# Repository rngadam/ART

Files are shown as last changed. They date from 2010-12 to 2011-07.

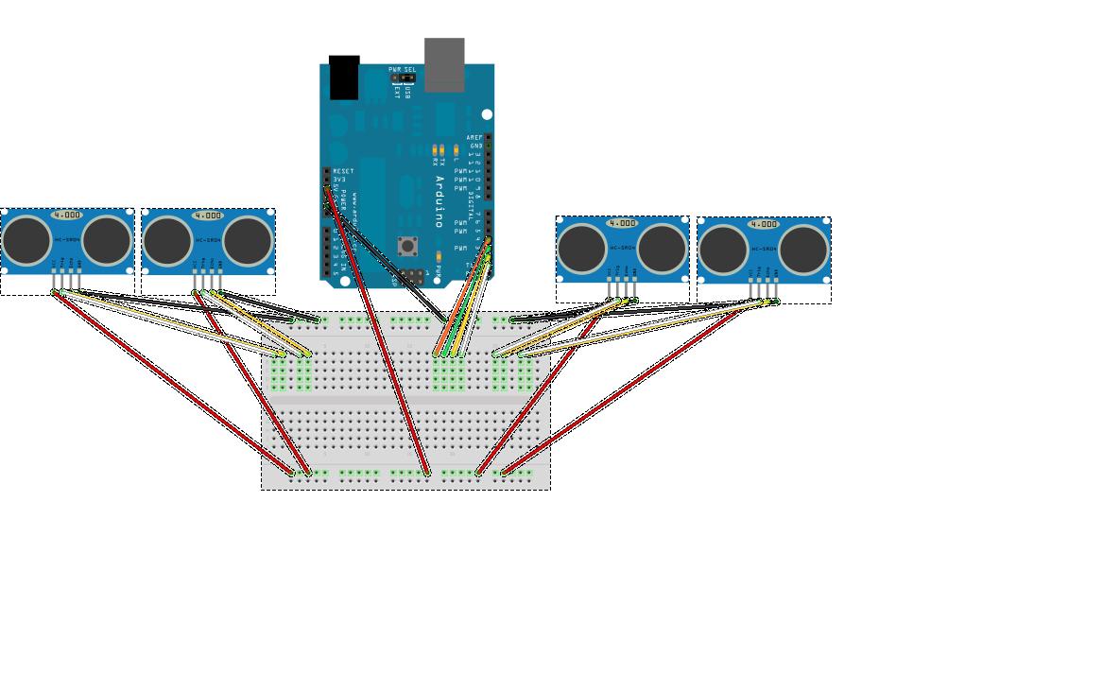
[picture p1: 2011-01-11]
ele/fritzing/ART-platform4_bb_20110103.jpg

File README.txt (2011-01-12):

Autonomous Robot Toy
http://www.xinchejian.com

Copyright 2011 Ricky Ng-Adam

   Licensed under the Apache License, Version 2.0 (the "License");
   you may not use this file except in compliance with the License.
   You may obtain a copy of the License at

       http://www.apache.org/licenses/LICENSE-2.0

   Unless required by applicable law or agreed to in writing, software
   distributed under the License is distributed on an "AS IS" BASIS,
   WITHOUT WARRANTIES OR CONDITIONS OF ANY KIND, either express or implied.
   See the License for the specific language governing permissions and
   limitations under the License.

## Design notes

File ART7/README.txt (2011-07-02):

Dependencies:

firmware:
	Arduino 22
	Android ADK release 0512

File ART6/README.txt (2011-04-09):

http://xinchejian.com

ART v6 (Autonomous Robot Toy)
Mechanical base: Remote control toy car
Motor control: microcontroller manipulation of the RC control
Sensors: five E18-D80NK infrared (obstacle detection, no distance ranging)
Computer: Arduino Uno
Characteristics: hacked inexpensive RC car, self-driving, forward and reverse fast interrupt-driven collision detection
Cost to build: ~425 RMB (~USD$65)
Code: https://github.com/rngadam/ART/tree/master/ART6
Video: http://v.youku.com/v_show/id_XMjU2NTQwMDky.html

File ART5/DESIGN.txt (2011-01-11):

ART5 (Autonomous Robot Toy version 5) combines the following:

- Mechanical four wheel vehicule based on a toy RC for propulsion and chassis
- Arduino Microcontroller  platform for communication and decisions
- CPLD for low-level sensor data acquisition and motor control
- RF communication to/from PC for debugging and visualization
- Processing-based dashboard on the PC.

RF communication solution is for telemetry and has been selected to be low-bandwidth, medium-range, low-power and inexpensive.

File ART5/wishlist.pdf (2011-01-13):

Receptacles

Type | Description | Details
Receptable Female Header 2.54mm DIP connector dual row | 9x2
Receptable Stackable Female Header 2.54mm DIP connector single row 8x1 Receptable Stackable Female Header 2.54mm DIP connector single row 6x1
Receptable DIP Socket Solder Tail | 18 pins
Receptable DIP Socket Solder Tail | 40 pins
Wires | Mini-JST Jumper cable (wires + male connector) | 2 wires
Wires | Mini-JST Jumper cable (wires + male connector) | 3 wires
Wires | Mini-JST Jumper cable (wires + male connector) | 4 wires
Wires | Mini-JST Jumper connector (female connector) | 2 wires
Wires | Mini-JST Jumper connector (female connector) | 3 wires
Wires | Mini-JST Jumper connector (female connector) | 4 wires
Connector
Wires | Heat-Shrink Tubing
Switch | Omron Snap Action Switch
Fastener | M3 nylon spacer
Fastener | M3 nylon screws
Fastener | M3 nylon washer
Fastener | M3 nylon nut
Fastener | M3 nylon standoff

Usage | Quantity | Example
RF transceiver RFC-1100A receptable | | http://www.alibaba.com/product-gs/283914360/Female_Header_2_54mm_DIP_connector/showimage.html
For custom Arduino shield | | http://www.alibaba.com/product-gs/285352058/2_54_mm_Single_Row_Female.html
For custom Arduino shield | | http://www.alibaba.com/product-gs/285352058/2_54_mm_Single_Row_Female.html
Socket for ATMega 328p | | http://toysdownunder.com/arduino/components/socket-plugs/18-pin-dip-socket.html
Socket for XC9536-DIP | | http://parts.digikey.com/1/parts/297142-40-pin-solder-tail-dip-socket-40-6518-10.html
Connect ground/vcc OR trigger/echo for HC-SR04
Connect ground/vcc/signal for infrared
Connect ground/vcc/trigger/echo
Connect ground/vcc OR trigger/echo for HC-SR04 Connect ground/vcc/signal for infrared
Connect ground/vcc/trigger/echo
Whiskers (collision detection) | | http://toysdownunder.com/arduino/components/action-switch.html
The spacers allows a constant gap between 2 components. http://www.bulte.com/gb/produits_fiche.cfm?id=1414&famille=entretoises

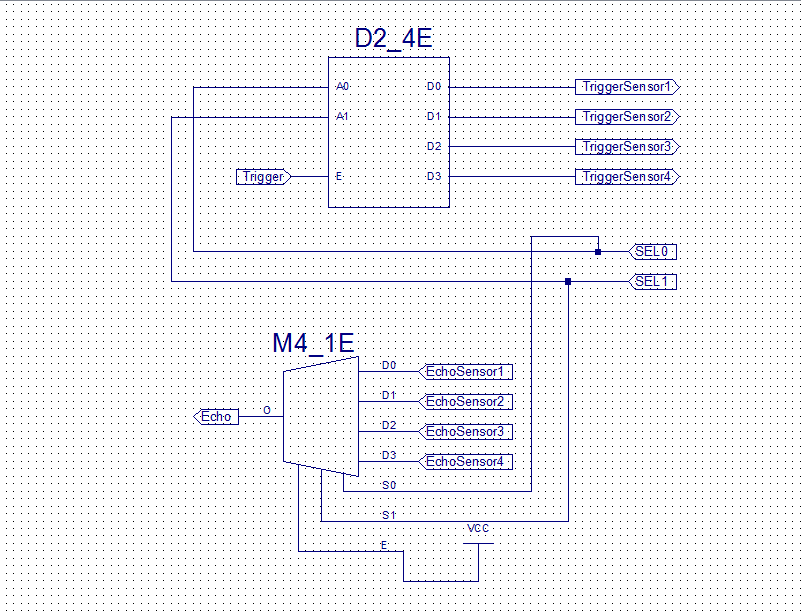
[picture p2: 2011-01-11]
ele/fritzing/UltrasonicDetector/schematic-sensor-selector.png

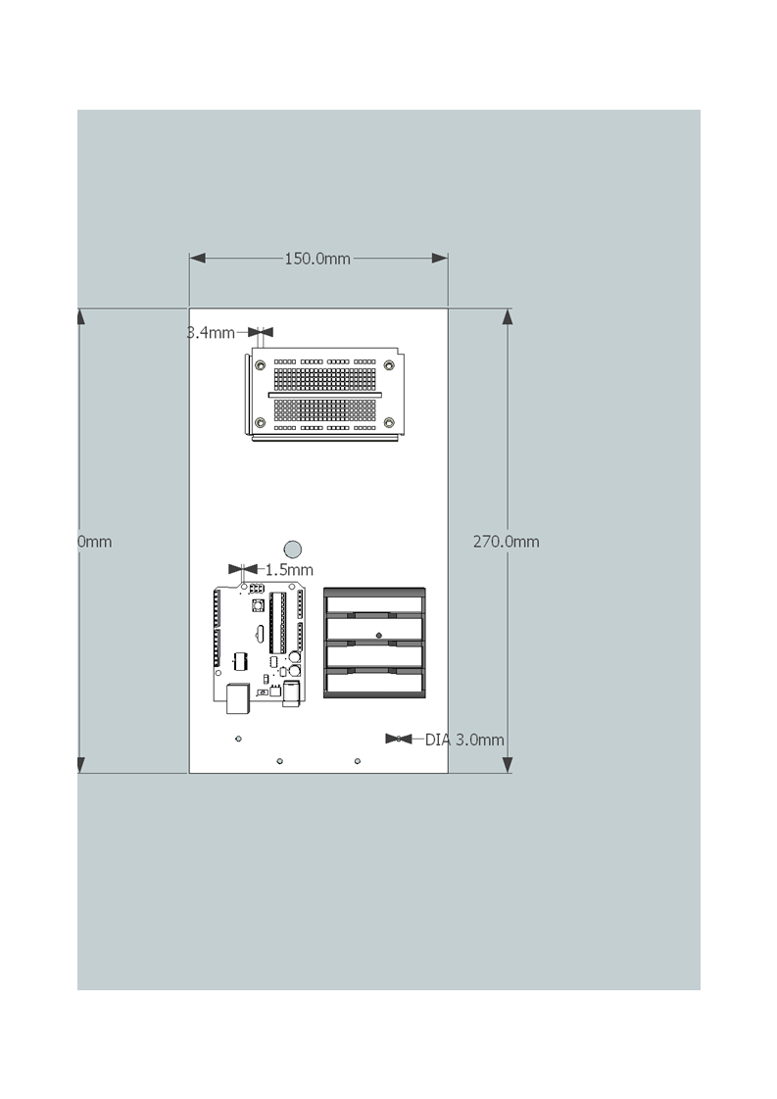
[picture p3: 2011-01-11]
mec/plate-v3_1.png

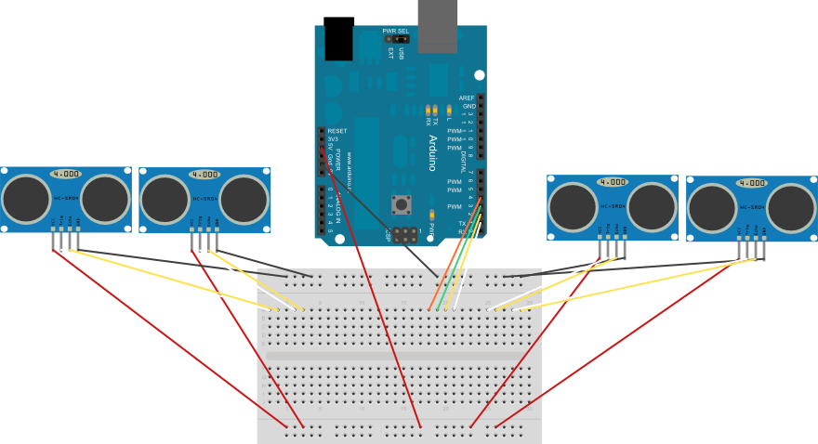
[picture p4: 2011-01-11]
ele/fritzing/ART-platform4_bb.png

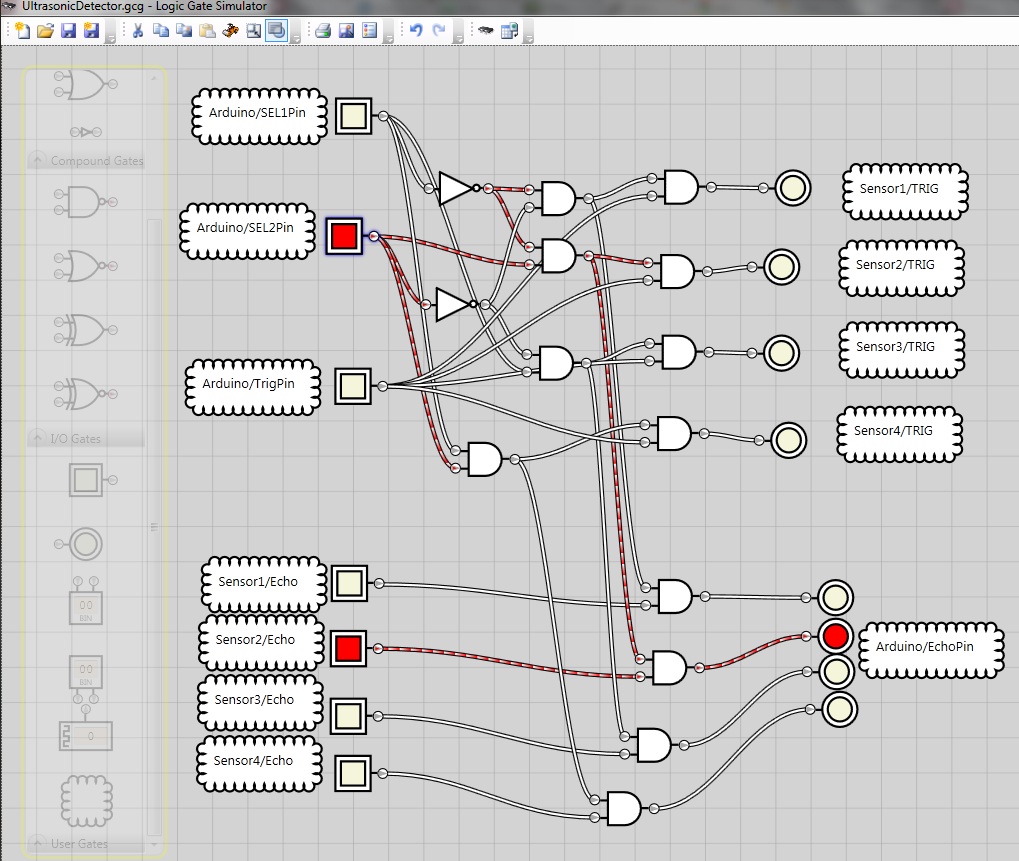
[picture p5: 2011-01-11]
ele/fritzing/UltrasonicDetector/UltrasonicDetectorLogic-LogicGateSimulator.jpg

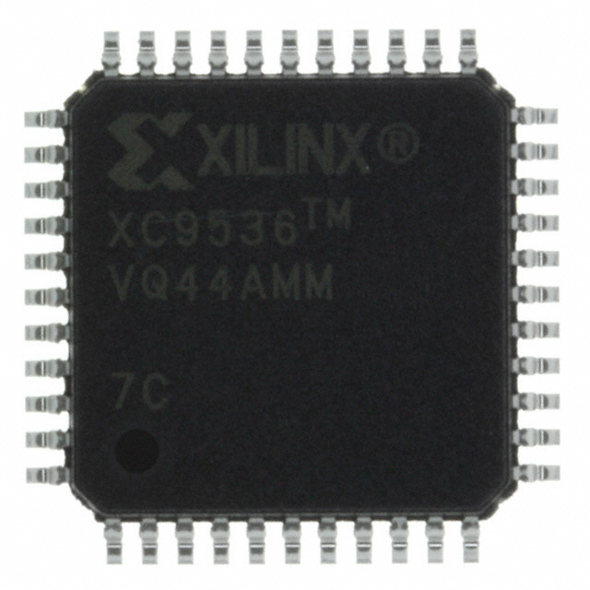
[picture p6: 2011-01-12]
ele/fritzing/XC9536-DIP/XC9536-7VQ44C.JPG

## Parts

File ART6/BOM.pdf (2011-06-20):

CAR

Description | Price/Unit | Quantity | Total
RC Toy Car (with 400mAh battery) | 67.00 | 1 | 67.00
Arduino Uno (with Atmega 328p) | 178.00 | 1 | 178.00
5 * Infrared sensors (E18-D80NK) | 30.00 | 5 | 150.00
Breadboard | 3.00 | 1 | 3.00
700mAh, 6V, Rechargeable NiCad | 15.00 | 1 | 15.00
Cabling and miscellaneous parts | 12.00 | 1 | 12.00
Total | | 64.3 | 425.00
| | USD | RMB

Source
http://item.taobao.com/item.htm?id=8549969961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

Datasheet

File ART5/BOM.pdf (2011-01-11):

CAR

Description | Price/Unit | Quantity | Total
RC Toy Car (with 400mAh battery) | 67.00 | 1 | 67.00
Arduino Uno (with Atmega 328p) | 178.00 | 1 | 178.00
CC1101 RF Transceiver with Power Amplifier | 70.00 | 1 | 70.00
4 * Ultrasonic sensors HC-SR04 | 37.00 | 4 | 148.00
4 * Infrared sensors E18-D80NK | 30.00 | 4 | 120.00
Xilinx XC9536 CPLD in a 40 DIP pin package | 42.00 | 1 | 42.00
Mini-breadboard | 3.00 | 1 | 3.00
700mAh, 6V, Rechargeable NiCad | 15.00 | 1 | 15.00
Cabling | 12.00 | 1 | 12.00
Motor shield (L298N) | 68.00 | 1 | 68.00
Arduino I/O expansion board | 48.00 | 1 | 48.00
Total | | 116.64 | 771.00
| | USD | RMB

Source
http://item.taobao.com/item.htm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

http://item.taobao.com/item.htm?id=8537476251http://item.taobao.com/item.htm?id=8537478635

Datasheet

http://iteadstudio.com/produce/cheap-cheap-ultrasonic-ranging-modulehc-sr04/

http://www.xilinx.com/support/documentation/xc9500.htm

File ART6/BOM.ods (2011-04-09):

Description | Price/Unit | Quantity | Total | Source | Datasheet
RC Toy Car (with 400mAh battery) | 67.00 | 1 | 67.00 | http://item.taobao.com/item.htm?id=7905841099
Arduino Uno (with Atmega 328p) | 178.00 | 1 | 178.00 | http://item.taobao.com/item.htm?id=8597883697
5 * Infrared sensors (E18-D80NK) | 30.00 | 5 | 150.00 | http://item.taobao.com/item.htm?id=8549969961
Breadboard | 3.00 | 1 | 3.00
700mAh, 6V, Rechargeable NiCad | 15.00 | 1 | 15.00
Cabling and miscellaneous parts | 12.00 | 1 | 12.00
Total |  | 64.3 | 425.00
 |  | USD | RMB

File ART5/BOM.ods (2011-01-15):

Description | Price/Unit | Quantity | Total | Source | Datasheet
RC Toy Car (with 400mAh battery) | 67.00 | 1 | 67.00 | http://item.taobao.com/item.htm?id=7905841099
Arduino Uno (with Atmega 328p) | 178.00 | 1 | 178.00 | http://item.taobao.com/item.htm?id=8597883697
RFC1100-A CC1101 RF Transceiver with Power Amplifier | 70.00 | 1 | 70.00 | http://item.taobao.com/item.htm?id=1914378907
4 * Ultrasonic sensors HC-SR04 | 37.00 | 4 | 148.00 | http://item.taobao.com/item.htm?id=3097091977 | http://iteadstudio.com/produce/cheap-cheap-ultrasonic-ranging-modulehc-sr04/
4 * Infrared sensors E18-D80NK | 30.00 | 4 | 120.00 | http://item.taobao.com/item.htm?id=8549969961
Xilinx XC9536 CPLD in a 40 DIP pin package | 42.00 | 1 | 42.00 | http://item.taobao.com/auction/item_detail.htm?item_num_id=5823204564 | http://www.xilinx.com/support/documentation/xc9500.htm
Mini-breadboard | 3.00 | 1 | 3.00
700mAh, 6V, Rechargeable NiCad | 15.00 | 1 | 15.00
Cabling | 12.00 | 1 | 12.00
Motor shield (L298N) | 68.00 | 1 | 68.00 | http://item.taobao.com/item.htm?id=8537476251
Arduino I/O expansion board | 48.00 | 1 | 48.00 | http://item.taobao.com/item.htm?id=8537478635
Total |  | 116.64 | 771.00
 |  | USD | RMB

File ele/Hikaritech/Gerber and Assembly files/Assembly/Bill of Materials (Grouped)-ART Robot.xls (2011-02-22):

Designator | Description | Comment | Footprint | Value | Quantity
C1 | Solid Aluminum Capacitor with Organic Semiconductor Electrolyte: 22uF, 25V, Bulk Pack | 25V | E | 22uF | 1
C2 | Solid Aluminum Capacitor with Organic Semiconductor Electrolyte: 100uF, 16V, Bulk Pack | 16V | E | 100uF | 1
C3, C4 | Dipped Radial Multilayer Ceramic Capacitor X7R: 100nF | VP41BY104 | VP41-2.5 | 100nF | 2
P1 | CONN 2 PINS 2.54mm Wire to Board Latch RA Tin | Battery Input | HDR1X2H |  | 1
P2, P3 | Header, 6-Pin | Arduino Header, Arduino Header Analog | HDR1X6 |  | 2
P4, P15 | Header, 8-Pin | Arduino Header Digital | HDR1X8 |  | 2
P5 | Header, 20-Pin, Dual row | CPLD Header DIP 40 | DIP-40 |  | 1
P6, P8, P10, P13 | CONN 3 PINS 2.54mm Wire to Board Latch RA Tin | IBH, IFH, ILH, IRH | HDR1X3H |  | 4
P7, P9, P11, P14 | CONN 4 PINS 2.54mm Wire to Board Latch RA Tin | UBH, UFH, ULH, URH | HDR1X4H |  | 4
P12, P17, P18, P19 | Header, 3-Pin | SBH, SFH, SLH, SRH | HDR1X3H |  | 4
P16 | Header, 9-Pin, Dual row | RFC-1100A | Module RF |  | 1
P20 | Header, 3-Pin, Dual row | Select | HDR2X3 |  | 1
R1, R2, R3, R4, R5, R6, R7 | Resistor | Res1 | AXIAL-0.3 | 1K | 7
U1 | Positive-Voltage Regulator | µA7805CKC | KC03 |  | 1

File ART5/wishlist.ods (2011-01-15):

Type | Description | Details | Usage | Quantity | Example
Receptable | Female Header 2.54mm DIP connector dual row | 9x2 | RF transceiver RFC-1100A receptable |  | http://www.alibaba.com/product-gs/283914360/Female_Header_2_54mm_DIP_connector/showimage.html
Receptable | Stackable Female Header 2.54mm DIP connector single row | 8x1 | For custom Arduino shield |  | http://www.alibaba.com/product-gs/285352058/2_54_mm_Single_Row_Female.html
Receptable | Stackable Female Header 2.54mm DIP connector single row | 6x1 | For custom Arduino shield |  | http://www.alibaba.com/product-gs/285352058/2_54_mm_Single_Row_Female.html
Receptable | DIP Socket Solder Tail | 18 pins | Socket for ATMega 328p |  | http://toysdownunder.com/arduino/components/socket-plugs/18-pin-dip-socket.html
Receptable | DIP Socket Solder Tail | 40 pins | Socket for XC9536-DIP |  | http://parts.digikey.com/1/parts/297142-40-pin-solder-tail-dip-socket-40-6518-10.html
Wires | Mini-JST Jumper cable (wires + male connector) | 2 wires | Connect ground/vcc OR trigger/echo for HC-SR04
Wires | Mini-JST Jumper cable (wires + male connector) | 3 wires | Connect ground/vcc/signal for infrared
Wires | Mini-JST Jumper cable (wires + male connector) | 4 wires | Connect ground/vcc/trigger/echo
Wires | Mini-JST Jumper connector (female connector) | 2 wires | Connect ground/vcc OR trigger/echo for HC-SR04
Wires | Mini-JST Jumper connector (female connector) | 3 wires | Connect ground/vcc/signal for infrared
Wires | Mini-JST Jumper connector (female connector) | 4 wires | Connect ground/vcc/trigger/echo
Connector
Wires | Heat-Shrink Tubing
Switch | Omron Snap Action Switch |  | Whiskers (collision detection) |  | http://toysdownunder.com/arduino/components/action-switch.html
Fastener | M3 nylon spacer |  | The spacers allows a constant gap between 2 components. |  | http://www.bulte.com/gb/produits_fiche.cfm?id=1414&famille=entretoises
Fastener | M3 nylon screws
Fastener | M3 nylon washer
Fastener | M3 nylon nut
Fastener | M3 nylon standoff

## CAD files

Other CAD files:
mec/robot-car-base-plate-with-arduino-v2.skp
mec/robot-car-base-plate-with-arduino-v3.skp
mec/robot-car-base-plate-with-arduino.skp
mec/robot-car-base-plate.skp

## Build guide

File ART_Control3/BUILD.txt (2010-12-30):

To build this robot toy car, you will need:

Components:

* an RC car (67RMB, http://item.taobao.com/item.htm?id=7905841099)
* an additional battery (to the one that comes with the RC car) rechargeable Ni-Cd 400mAh/6V battery pack 
* an Arduino (any should do, we use the Dueminalove)
* a pile of cables with pins
* one or more ranging sensor of some kind (infrared such as Sharp IR or Ultrasonic such as the Parallax Ping or both)
* a small breadboard
* an IC with at least 4 transistors (such as the ULN2803APG) or 4 separate NPN transistors 
* two AA battery (to test the RF transmitter)

Tools:
* a USB cable (standard USB transfer cable)
* a PC (Mac, Linux or Windows)
* Arduino software
* a Dremel (or its Chinese copy equivalent...)
* a wire stripper
* a marker (Sharpie fine point permanent marker)
* a right angle ruler
* a set of precision screwdrivers
* some electric tape (or alternatively, little name stickers...)
* four plastic bags for the screws you'll remove
* a soldering iron 
* a ballpen
* cardboard box at least 15cm X 25cm (surface to put the woodboard on top to drill holes)
* a camera for posterity!

Optional
* possibly a small servo-motor to rotate ranging sensor

Steps:

Charge your batteries 
* move to the next few steps that don't require battery while you wait (4 hours charge time)

Remove the plastic shell from the top of the car
* Turn over and start unscrewing starting with the back of the car
* Note that you may have to unscrew at an angle to get the screws furthest back out
* Keep the screws securely in a bag, organized by step (write down where they came from with the marker)
* You will find 4 screws on the main plate, 2 in front, 2 for the lights
* Get the antenna out of the shell (don't pull out too quickly - watch out for those thin wires connecting to the light)
* Put the shell on the side
* Remove the hot glue by melting it with soldering iron and a pair of tweezers 
* Remove the useless soundbox plastic cover box on top of the servo (3 screws)
* Screw the lights upside-down on the servo plastic box now available holes
* Tape the electric wires from the light to the plastic chassis

Test your car with the provided RF remote to verify that it does indeed still work

Take apart the remote
* twist the round plastic piece securing the antenna
* remove screws to open the case (6 screws)
* remove the screws holding down the board
* take care to mark which wire goes to source and ground (ex: the wire to positive marked the marker)
* unscrew the antenna

Create a new wood plate by tracing the various components and holes (don't forget the hole for the antenna)
* Dimension: 15cm wide by 25cm long (size of wood board is chosen to fit the board within the wheels)
* Use the right angle ruler: create an angle, measure desired width and height, trace box with marker

Remove the plastic plate on which the plastic shell was screwed
* Remove the four screws and then squeeze the hinges on the front of the plate to remove

Do the layout
* Figure out where to put the holes by overlaying the plastic plate on the board 
* To locate holes, remove the ballpoint from the pen body  
* Take all the electric components and place them on the new plate until satisfied with the layout
* Trace screwholes and the outline of parts for electronics
* Don't forget to leave a larger hole on the front of the plastic plate and to the left for the antenna to come out!
* Create a grid of holes in front and in the back of the board to give you flexibility in placing the sensors

Cut the wood plate with the dremel
* Cut rectangle with the Dremel and than break if off
* Sand edges of rectangle

Drill holes into the wood plate with the dremel 
* use a spare piece of wood or cardboard box upside-down
* put the wood board on the cardboard box
* drill holes!
* Verify alignment with plastic plate of chassis
* Test alignment with antenna

Assemble mechanical parts
* Put back the plastic plate on the car
* Tie-wrap the wood board to the plastic plate
* Tie-wrap the components to the wood board

Assemble electronics
* Connect wires to/from the various components (except the battery)
* Strip the wire from the transmitter and push the wire filaments in the breadboard using the wires with pin
* If possible, use consistent wires (white or yellow for signal, black or blue for ground, red or orange for power)

Place the sensor(s)
* Make sure the sensors are physically secure (they tend to move when the robot hit something...)

Write basic Arduino program
* Start Arduino IDE
* Write basic Arduino program
* Connect to USB
* Upload

Test your robot
* transmitter light comes on 
* sensor obstacle detection works
* Test that motor control works
* Turn on the car, manually trigger the sensor
* Put it on the ground and let it fly! (don't forget to get it on video!)

Next step
* Use version control (github.com or code.google.com) to keep source and documentation
* When a version (kinda) does something interesting, commit to source control and explain observed behavior
                
Future
* Mount electronic parts on motherboard stands (?)
* Create a working RF transmitter that can talk to the receiver
* Design and get PCB done (integrating power connection, switches, etc)
* Design and get aluminium plate done

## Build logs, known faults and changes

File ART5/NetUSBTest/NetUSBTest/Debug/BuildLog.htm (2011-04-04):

Build Log

| | Build started: Project: NetUSBTest, Configuration: Debug|Win32

Command Lines

Creating temporary file "c:\Users\rngadam\ART\ART5\NetUSBTest\NetUSBTest\Debug\RSP00000540082868.rsp" with contents
[
/Od /D "WIN32" /D "_DEBUG" /D "_CONSOLE" /D "_UNICODE" /D "UNICODE" /Gm /EHsc /RTC1 /MDd /Yu"stdafx.h" /Fp"Debug\NetUSBTest.pch" /Fo"Debug\\" /Fd"Debug\vc90.pdb" /W3 /c /ZI /TP .\NetUSBTest.cpp
]
Creating command line "cl.exe @c:\Users\rngadam\ART\ART5\NetUSBTest\NetUSBTest\Debug\RSP00000540082868.rsp /nologo /errorReport:prompt"
Creating temporary file "c:\Users\rngadam\ART\ART5\NetUSBTest\NetUSBTest\Debug\RSP00000640082868.rsp" with contents
[
/OUT:"C:\Users\rngadam\ART\ART5\NetUSBTest\Debug\NetUSBTest.exe" /INCREMENTAL /MANIFEST /MANIFESTFILE:"Debug\NetUSBTest.exe.intermediate.manifest" /MANIFESTUAC:"level='asInvoker' uiAccess='false'" /DEBUG /PDB:"c:\Users\rngadam\ART\ART5\NetUSBTest\Debug\NetUSBTest.pdb" /SUBSYSTEM:CONSOLE /DYNAMICBASE /NXCOMPAT /MACHINE:X86 kernel32.lib user32.lib gdi32.lib winspool.lib comdlg32.lib advapi32.lib shell32.lib ole32.lib oleaut32.lib uuid.lib odbc32.lib odbccp32.lib

".\Netusb.lib"

".\Debug\NetUSBTest.obj"

".\Debug\stdafx.obj"

".\Debug\NetUSBTest.exe.embed.manifest.res"
]
Creating command line "link.exe @c:\Users\rngadam\ART\ART5\NetUSBTest\NetUSBTest\Debug\RSP00000640082868.rsp /NOLOGO /ERRORREPORT:PROMPT"
Creating temporary file "c:\Users\rngadam\ART\ART5\NetUSBTest\NetUSBTest\Debug\RSP00000740082868.rsp" with contents
[
/out:.\Debug\NetUSBTest.exe.embed.manifest /notify_update /manifest

.\Debug\NetUSBTest.exe.intermediate.manifest
]
Creating command line "mt.exe @c:\Users\rngadam\ART\ART5\NetUSBTest\NetUSBTest\Debug\RSP00000740082868.rsp /nologo"
Creating temporary file "c:\Users\rngadam\ART\ART5\NetUSBTest\NetUSBTest\Debug\BAT00000840082868.bat" with contents
[
@echo Manifest resource last updated at %TIME% on %DATE% > .\Debug\mt.dep
]
Creating command line "c:\Users\rngadam\ART\ART5\NetUSBTest\NetUSBTest\Debug\BAT00000840082868.bat"

Output Window

Compiling...
NetUSBTest.cpp
c:\users\rngadam\art\art5\netusbtest\netusbtest\netusbtest.cpp(3) : warning C4603: 'WIN32_LEAN_AND_MEAN' : macro is not defined or definition is different after precompiled header use
Add macro to precompiled header instead of defining here
c:\users\rngadam\art\art5\netusbtest\netusbtest\netusbtest.cpp(4) : use of precompiled header
c:\users\rngadam\art\art5\netusbtest\netusbtest\netusbtest.cpp(37) : warning C4018: '<' : signed/unsigned mismatch
c:\users\rngadam\art\art5\netusbtest\netusbtest\netusbtest.cpp(86) : warning C4101: 'result' : unreferenced local variable
c:\users\rngadam\art\art5\netusbtest\netusbtest\netusbtest.cpp(118) : warning C4101: 'mesg' : unreferenced local variable
Linking...
Embedding manifest...

Results

| | Build Time 0:01 Build log was saved at "file://c:\Users\rngadam\ART\ART5\NetUSBTest\NetUSBTest\Debug\BuildLog.htm" NetUSBTest - 0 error(s), 4 warning(s)

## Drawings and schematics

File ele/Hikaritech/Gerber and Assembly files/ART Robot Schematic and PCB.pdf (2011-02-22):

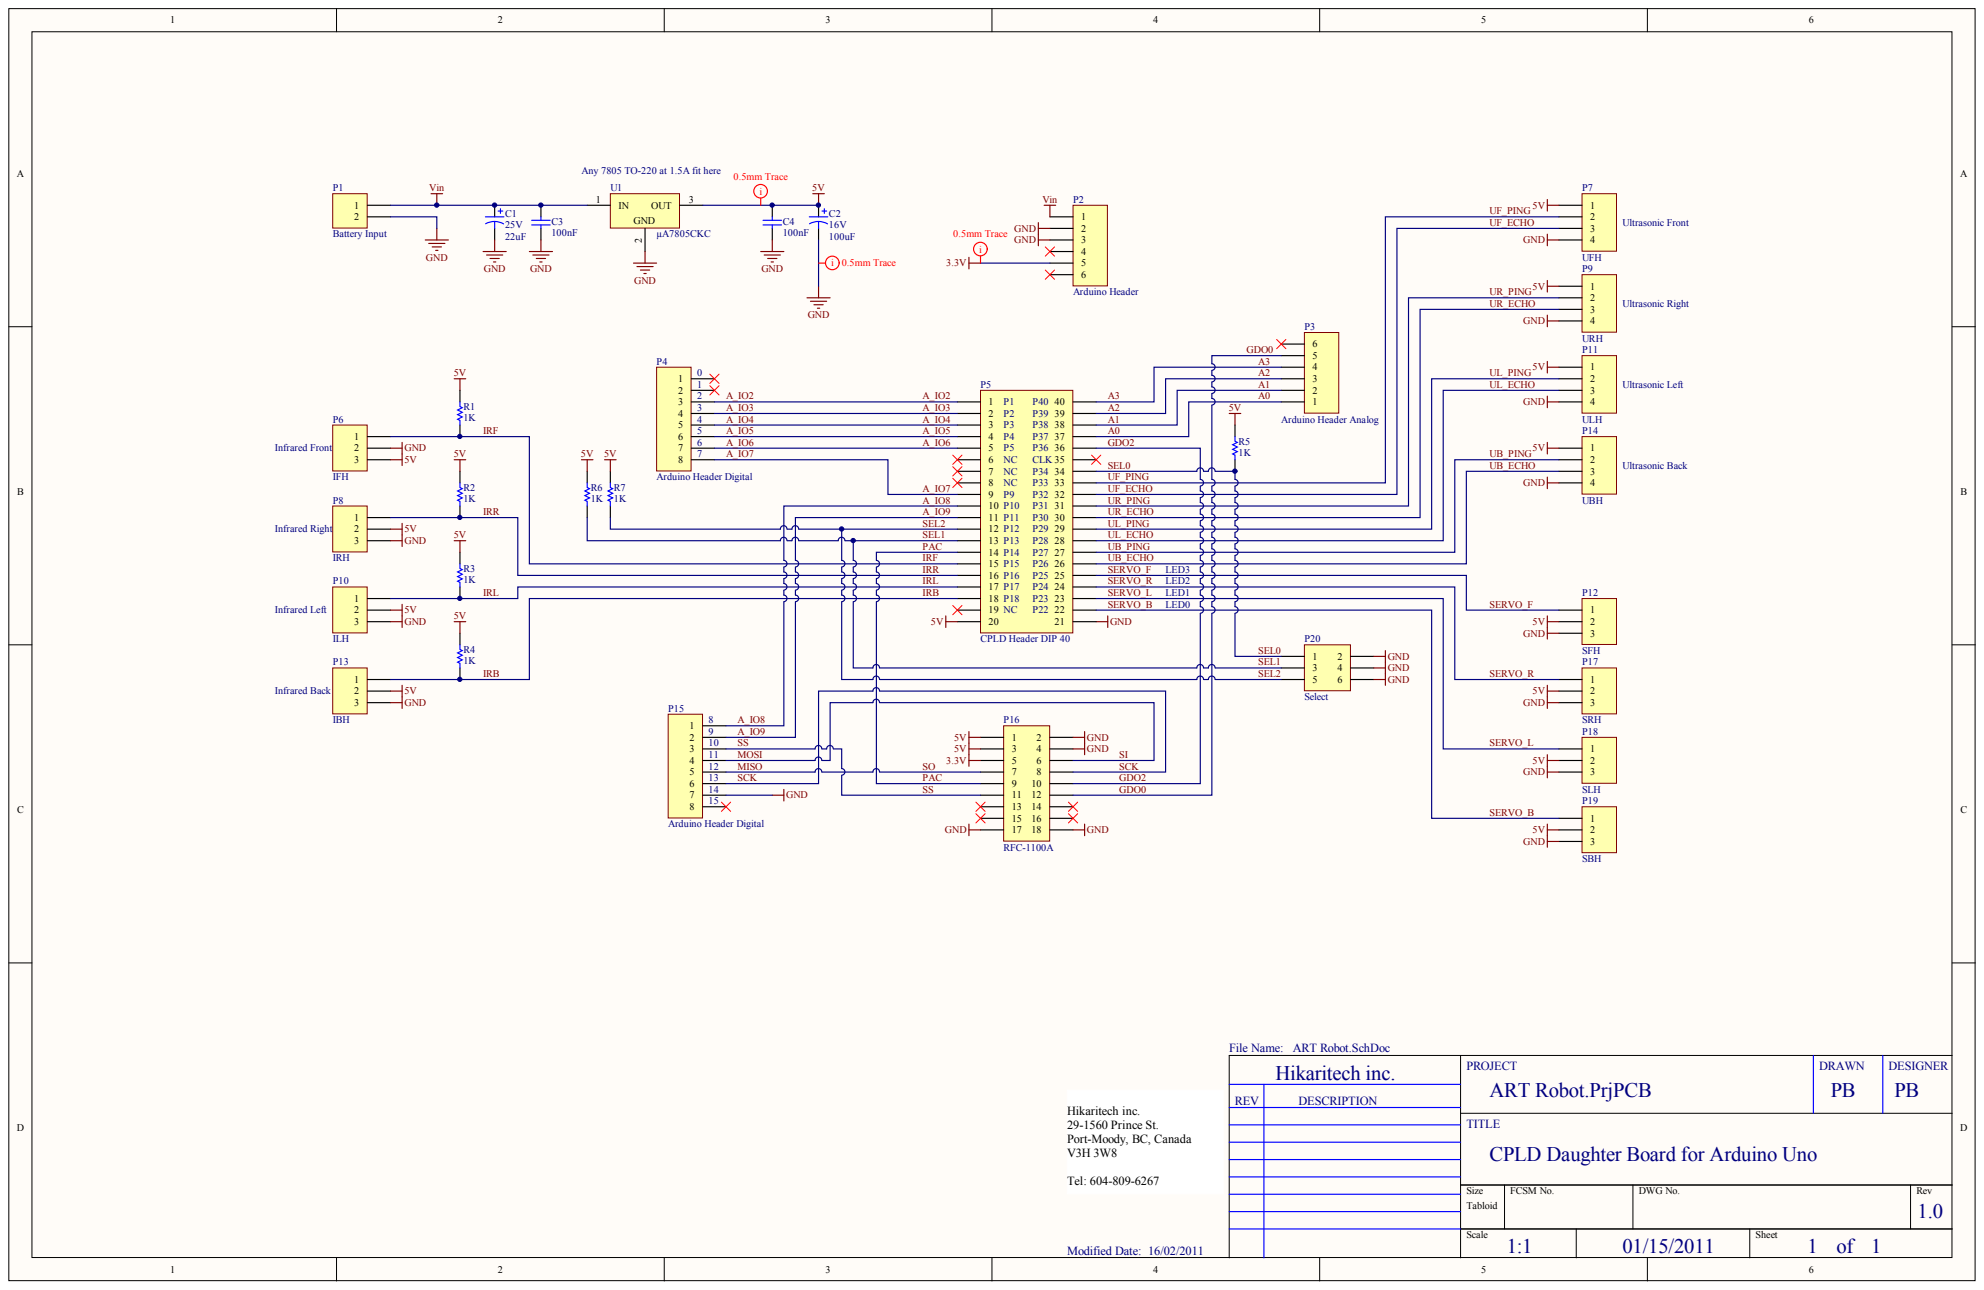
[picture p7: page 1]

UR_ECH O

A_ IO3 | | 5 V
A_ IO4 | A 1

5 V 5 V 5 V K K | A_ IO6 | GDO 2 | R5 1 K

UF _ P ING | GND
UF _ECH O

5 V | | S EL2 | UL_ P ING

S EL1 | | UL_ECH O
P A C | | UB_ P ING

S ERVO_ R LED2

1 2 | MI S O | | S O | | 7 8 | | | S C K
1 3 | S C K | | P A C | 9 1 0 1 1 1 2 1 3 1 4 1 5 1 6 1 7 1 8 | | | GDO 2
1 4 | | S S | | | | GDO 0

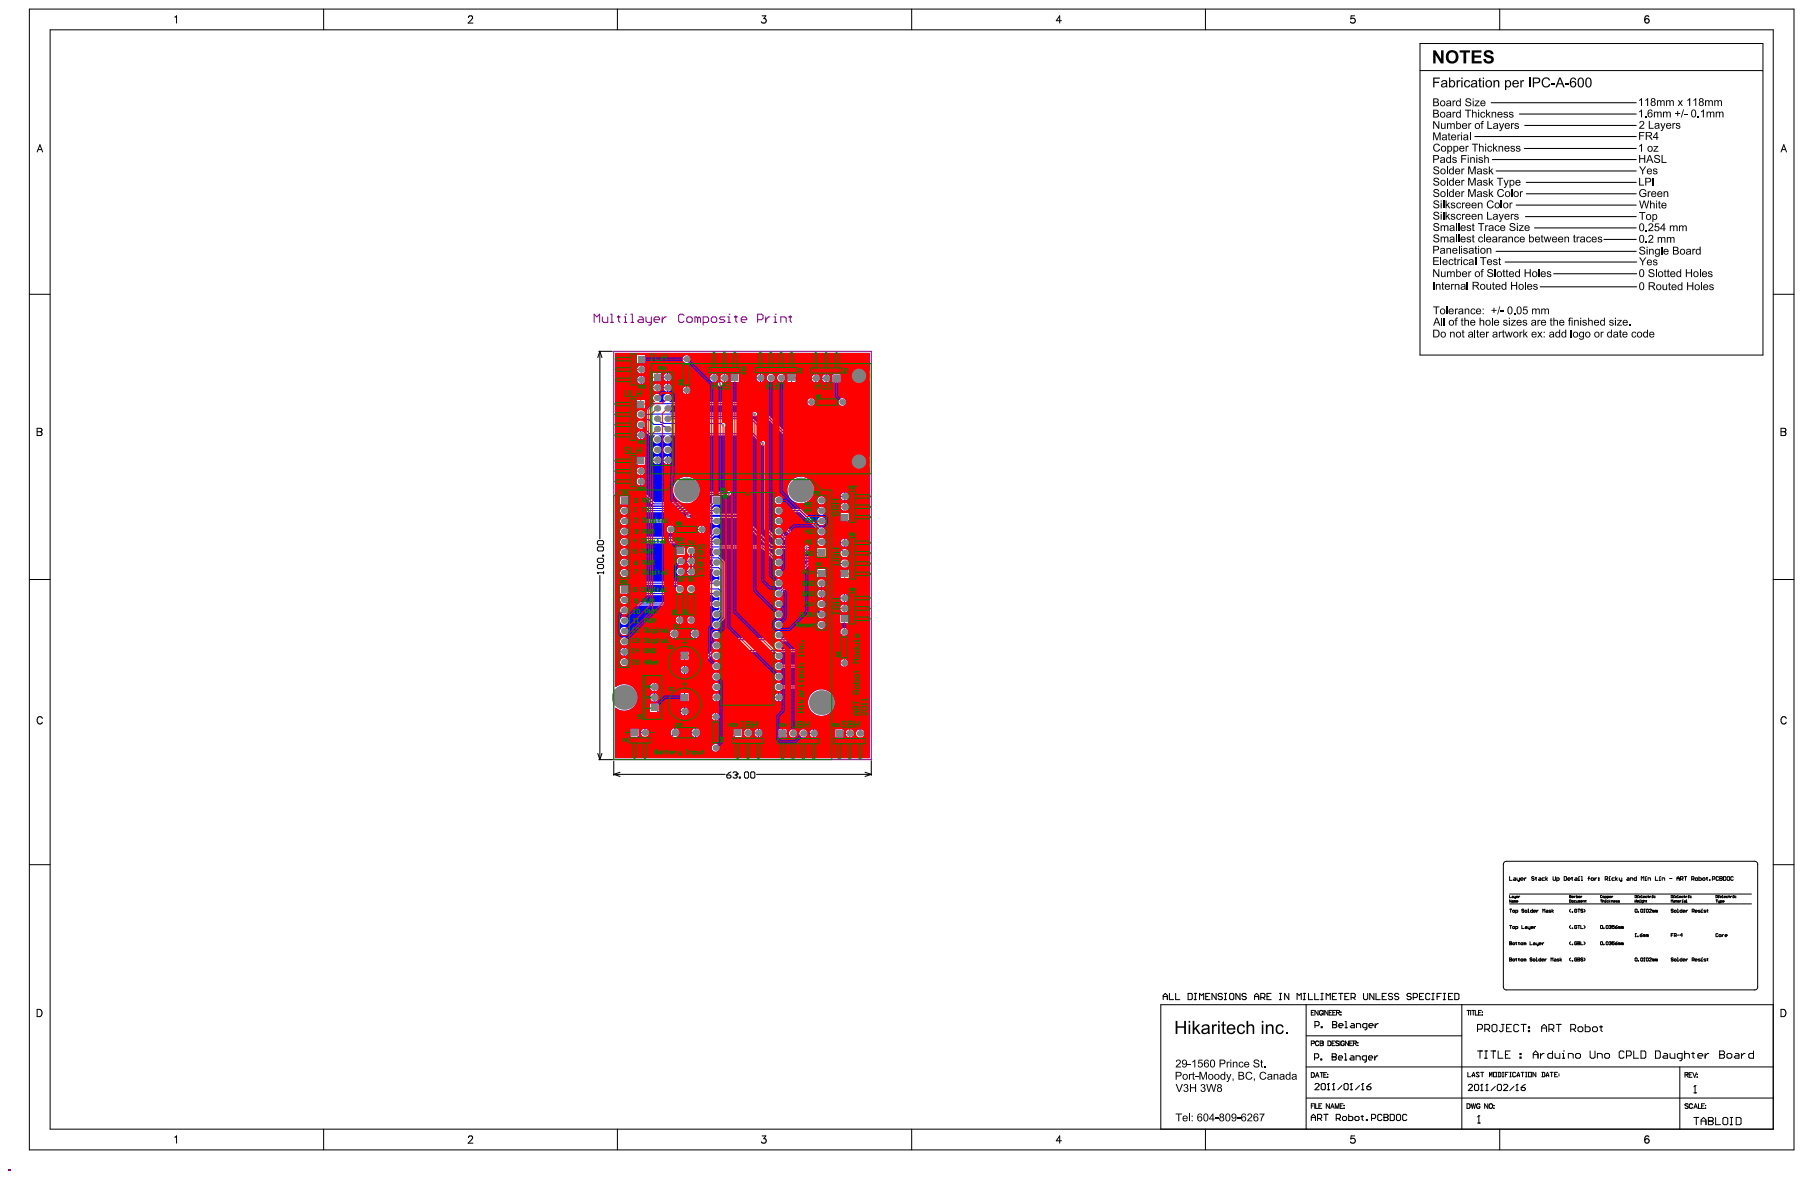
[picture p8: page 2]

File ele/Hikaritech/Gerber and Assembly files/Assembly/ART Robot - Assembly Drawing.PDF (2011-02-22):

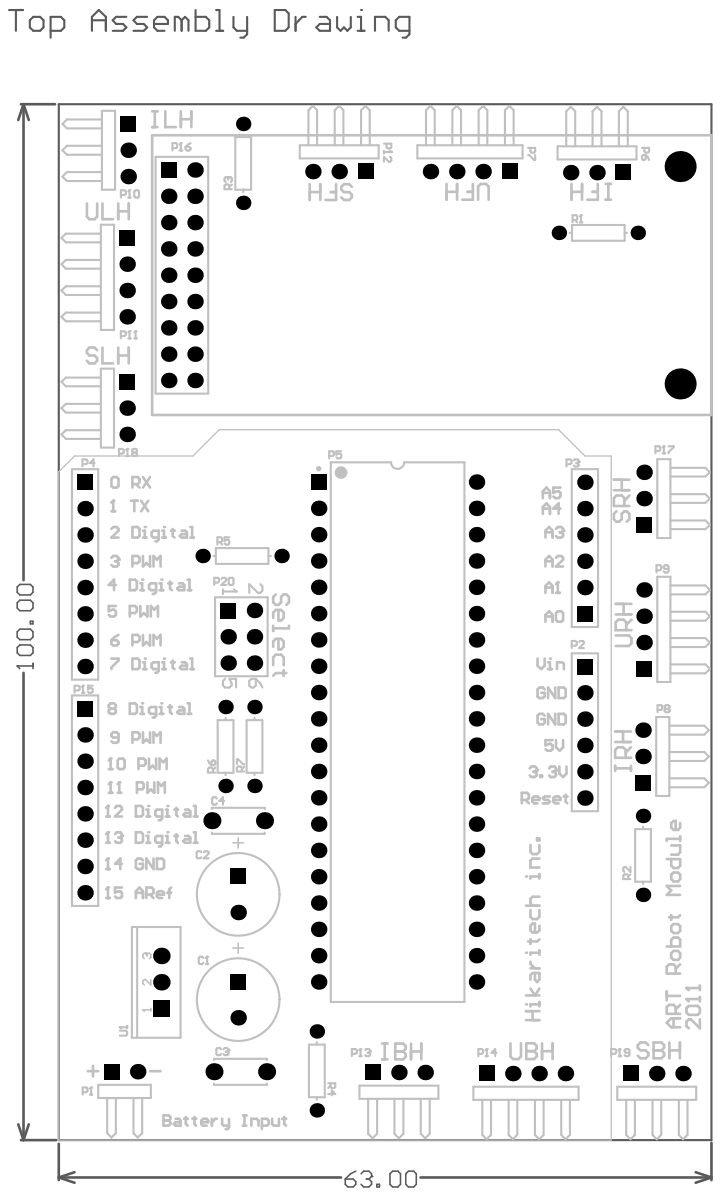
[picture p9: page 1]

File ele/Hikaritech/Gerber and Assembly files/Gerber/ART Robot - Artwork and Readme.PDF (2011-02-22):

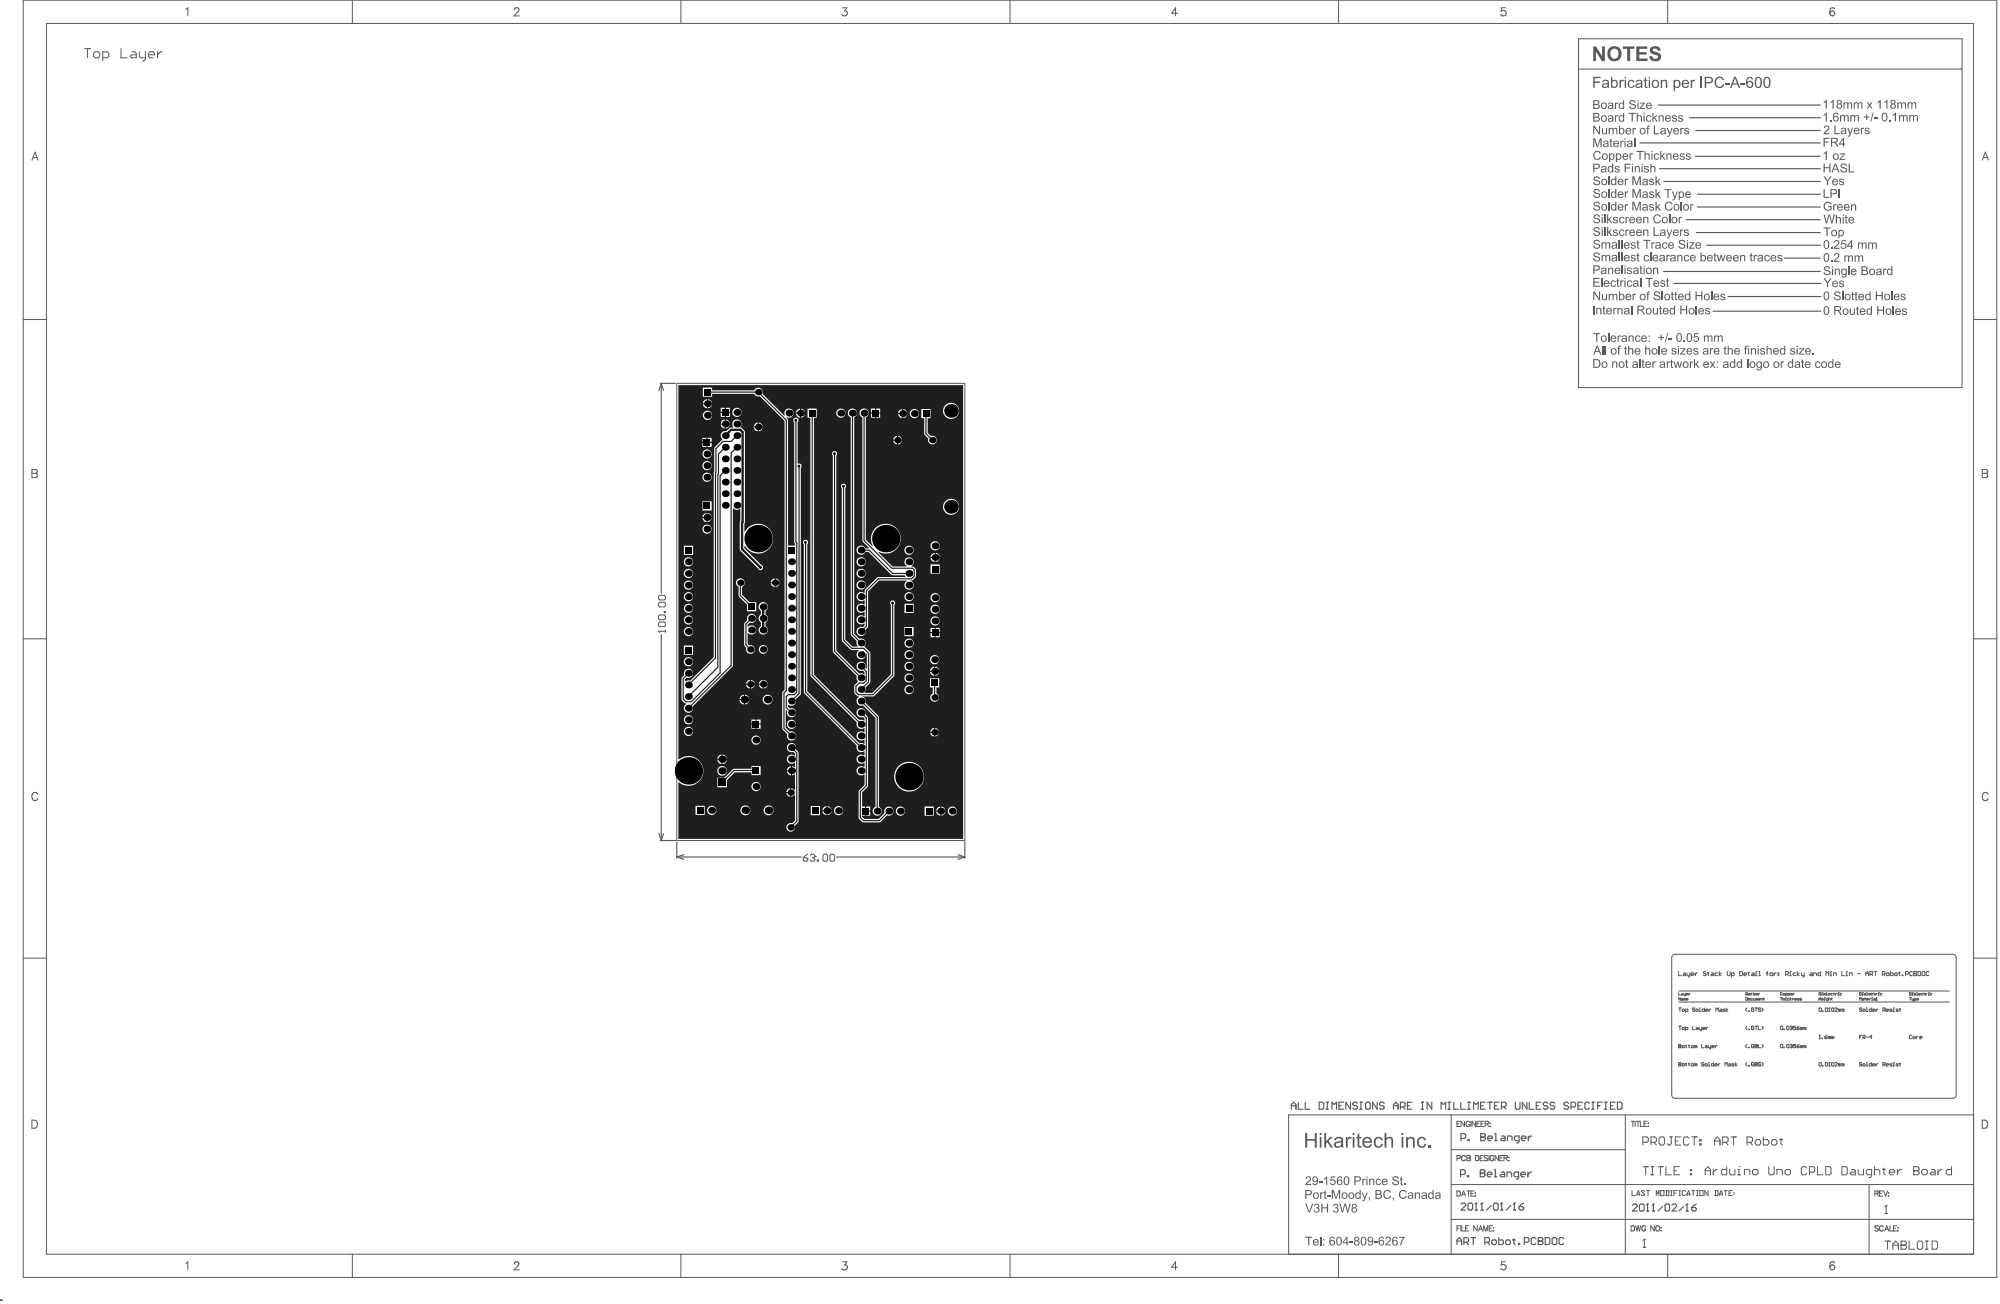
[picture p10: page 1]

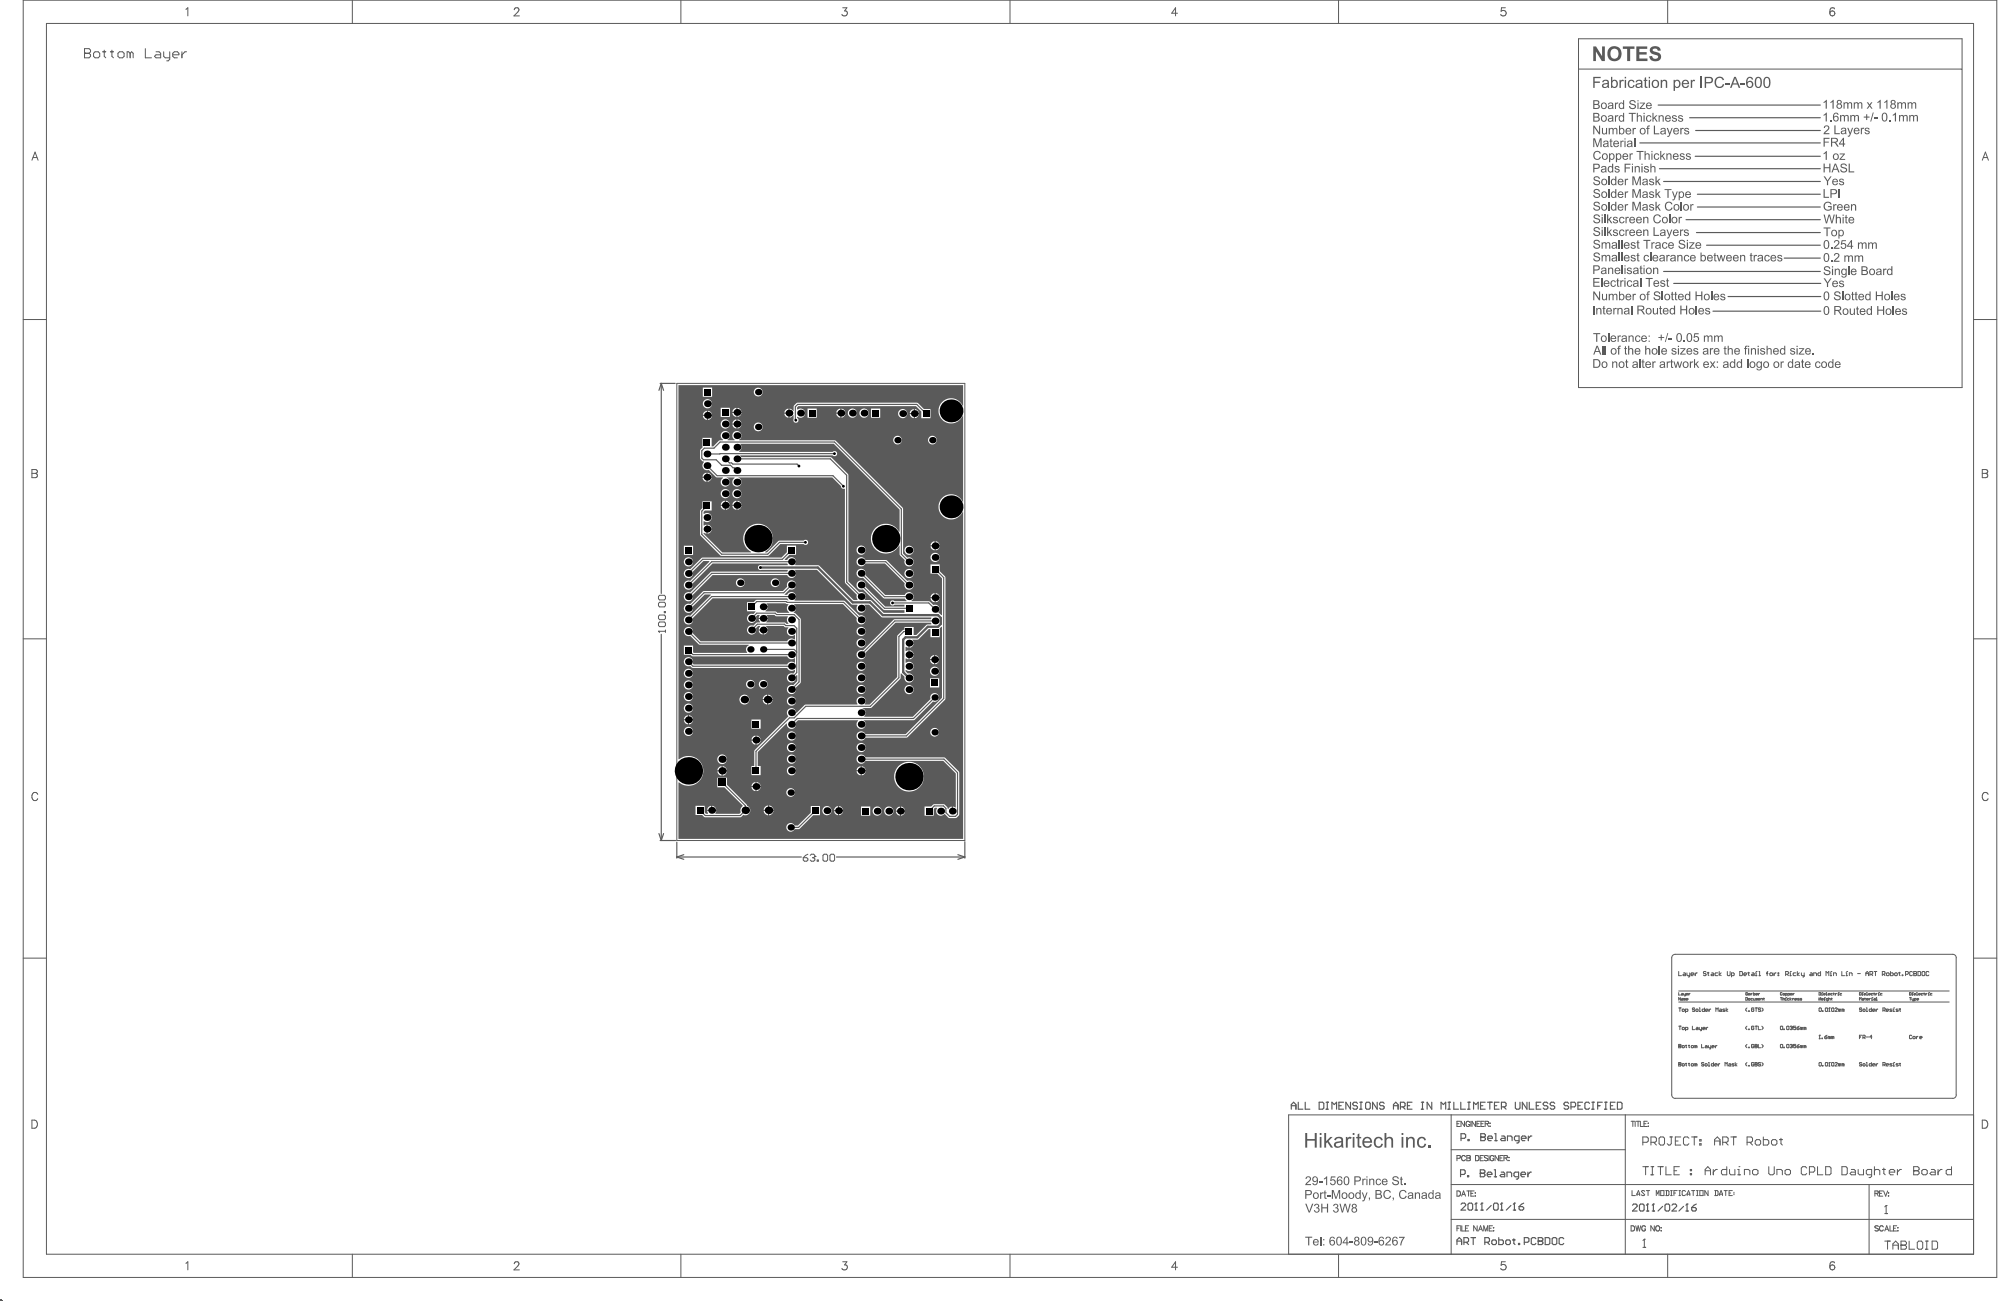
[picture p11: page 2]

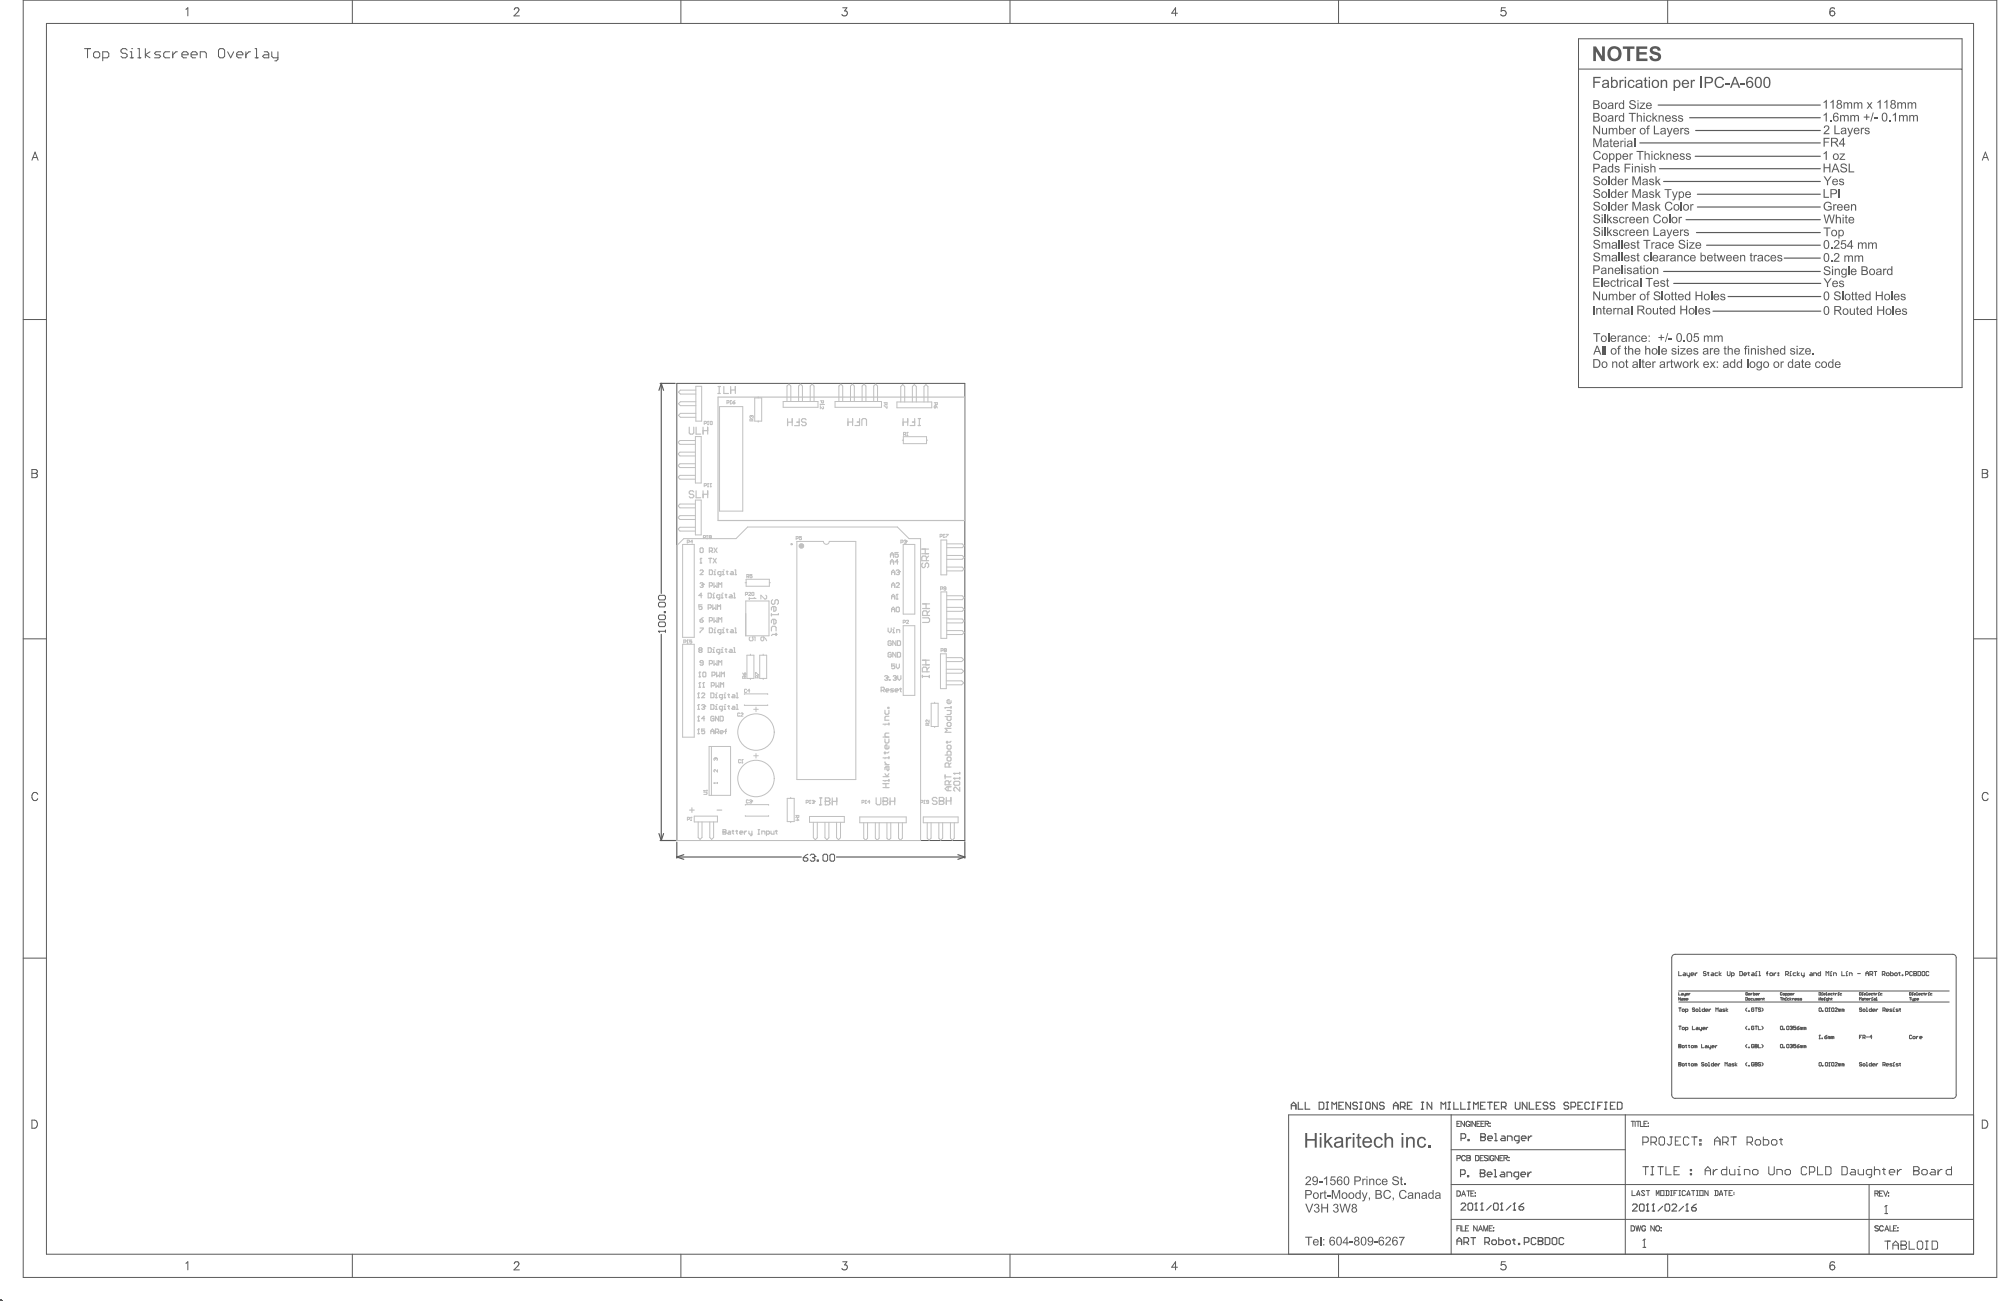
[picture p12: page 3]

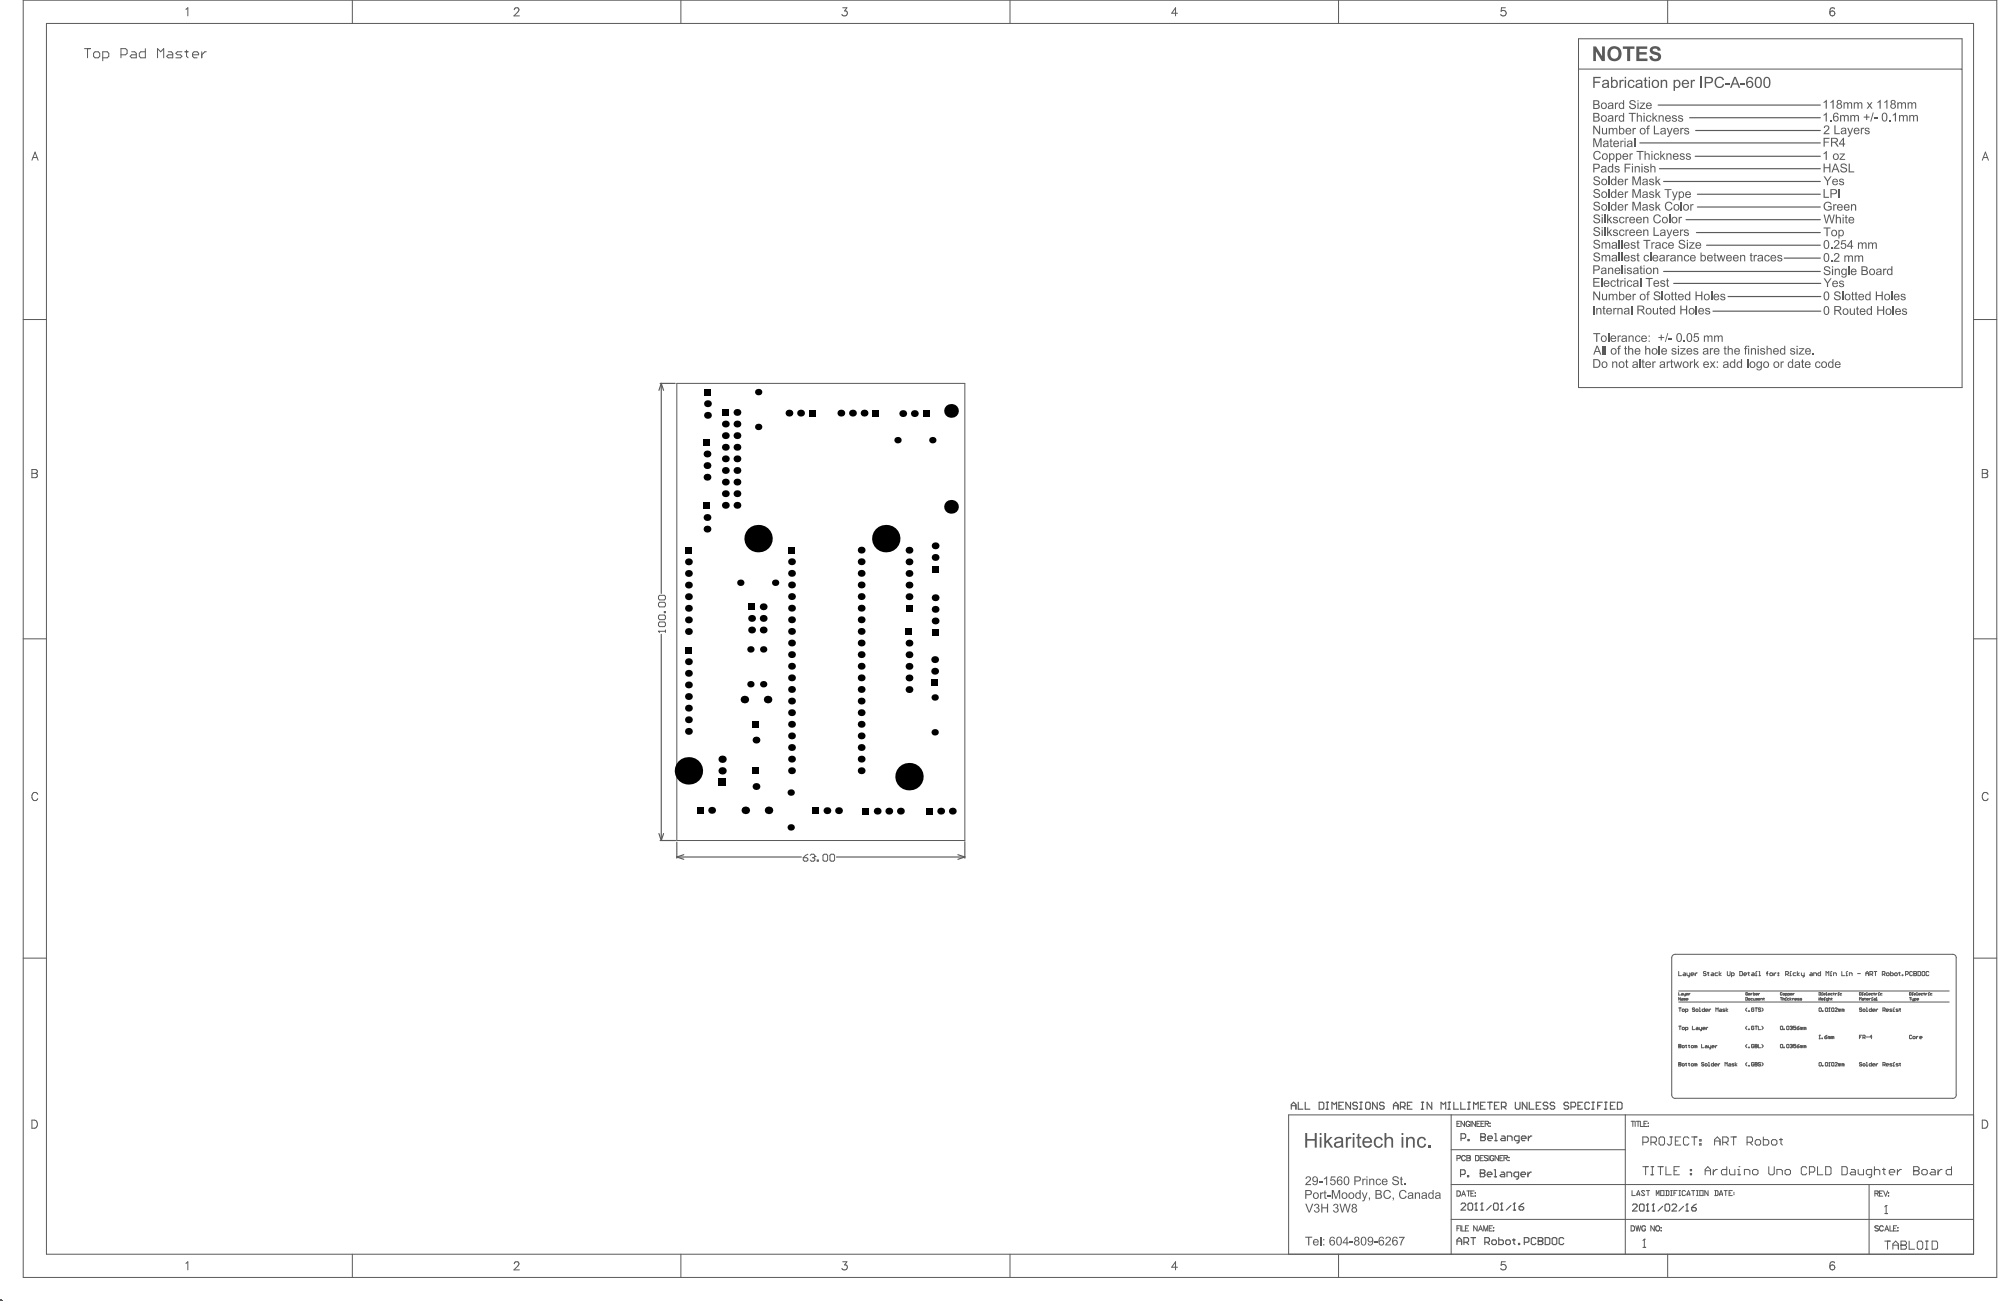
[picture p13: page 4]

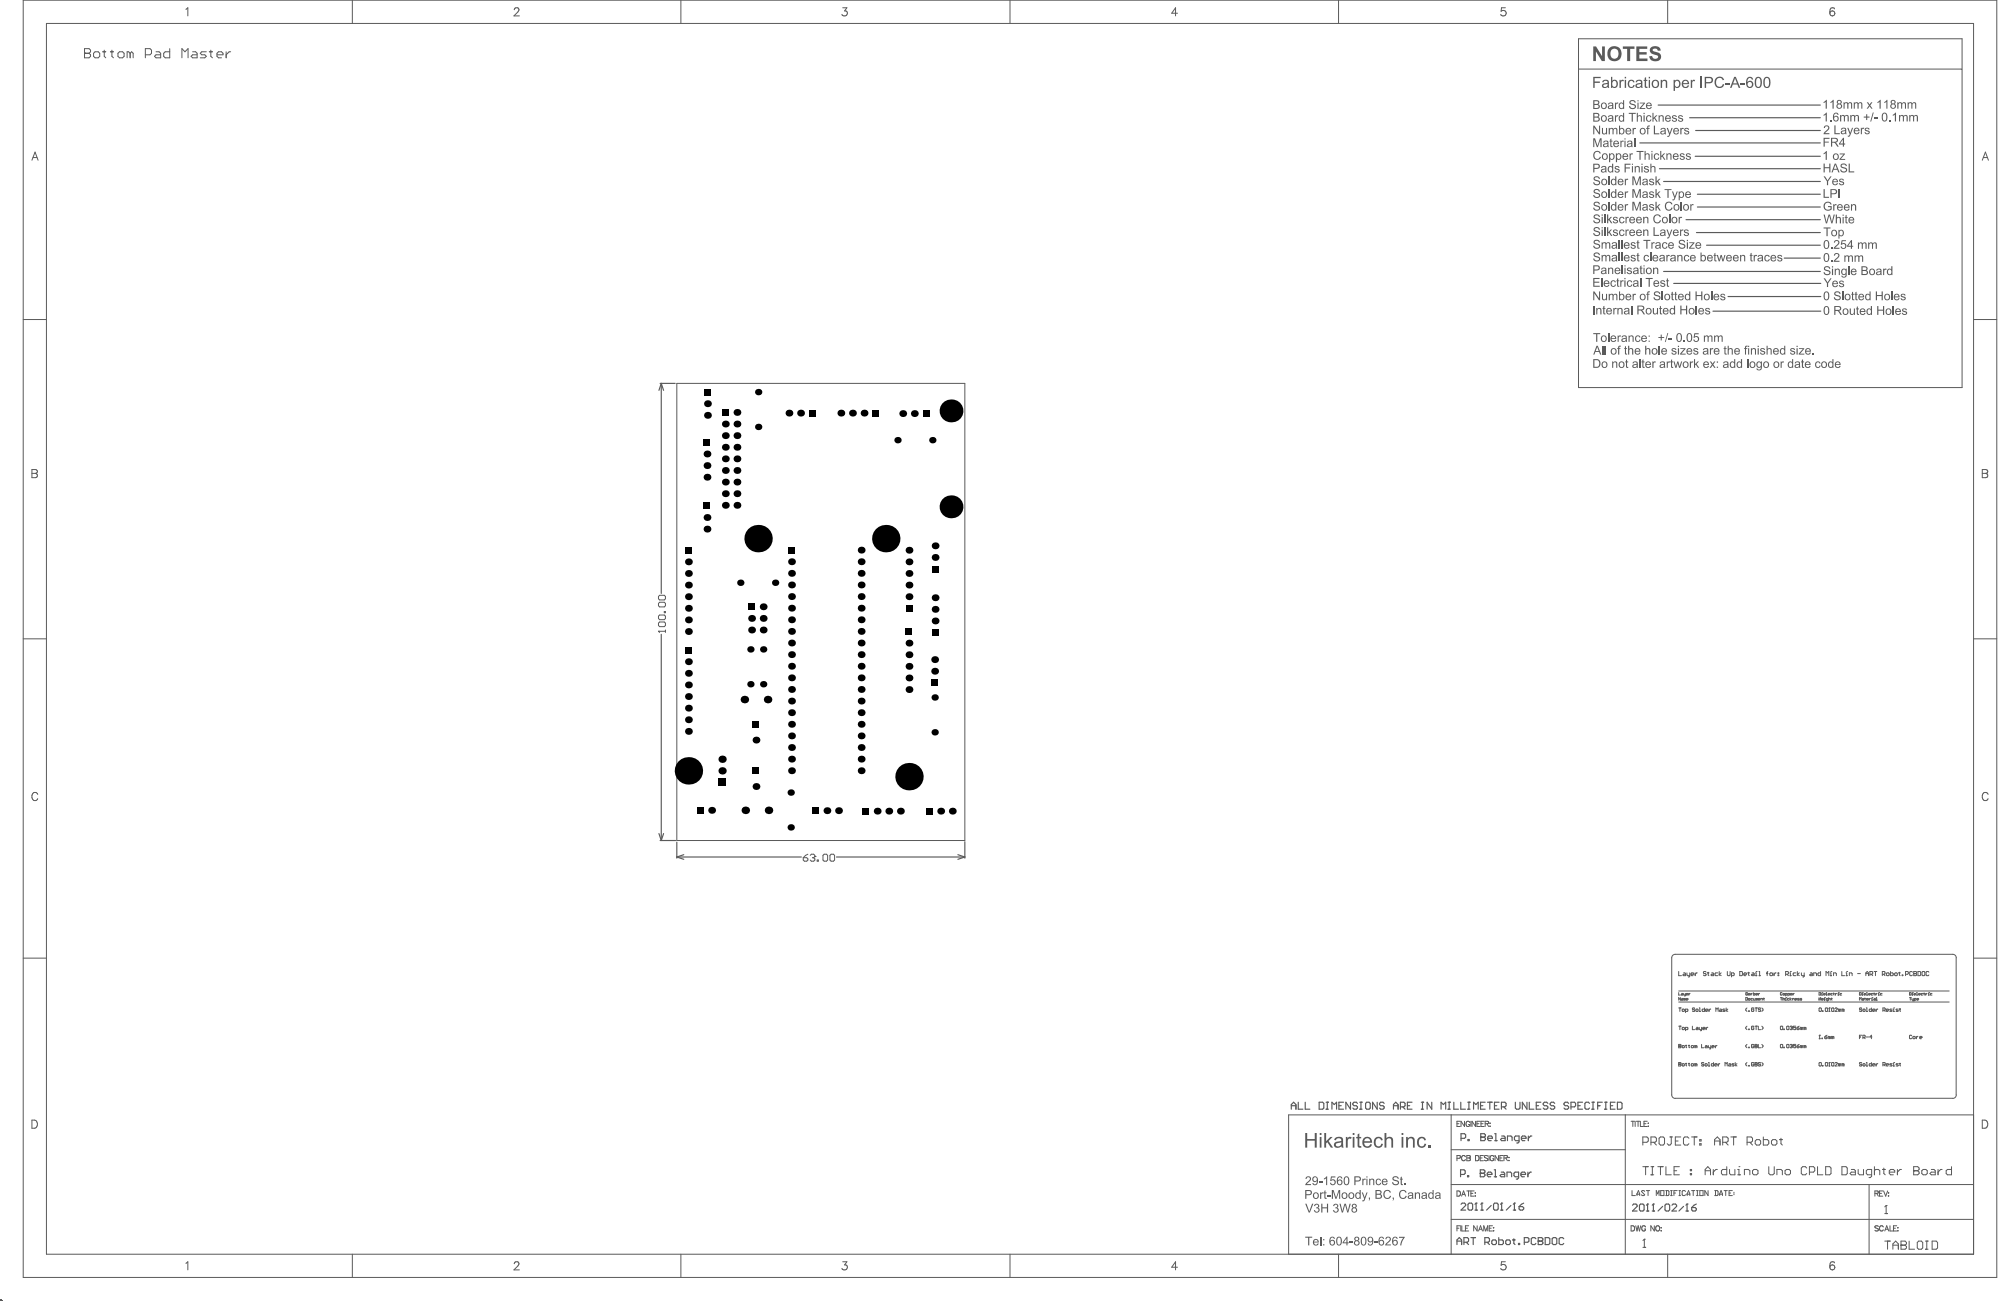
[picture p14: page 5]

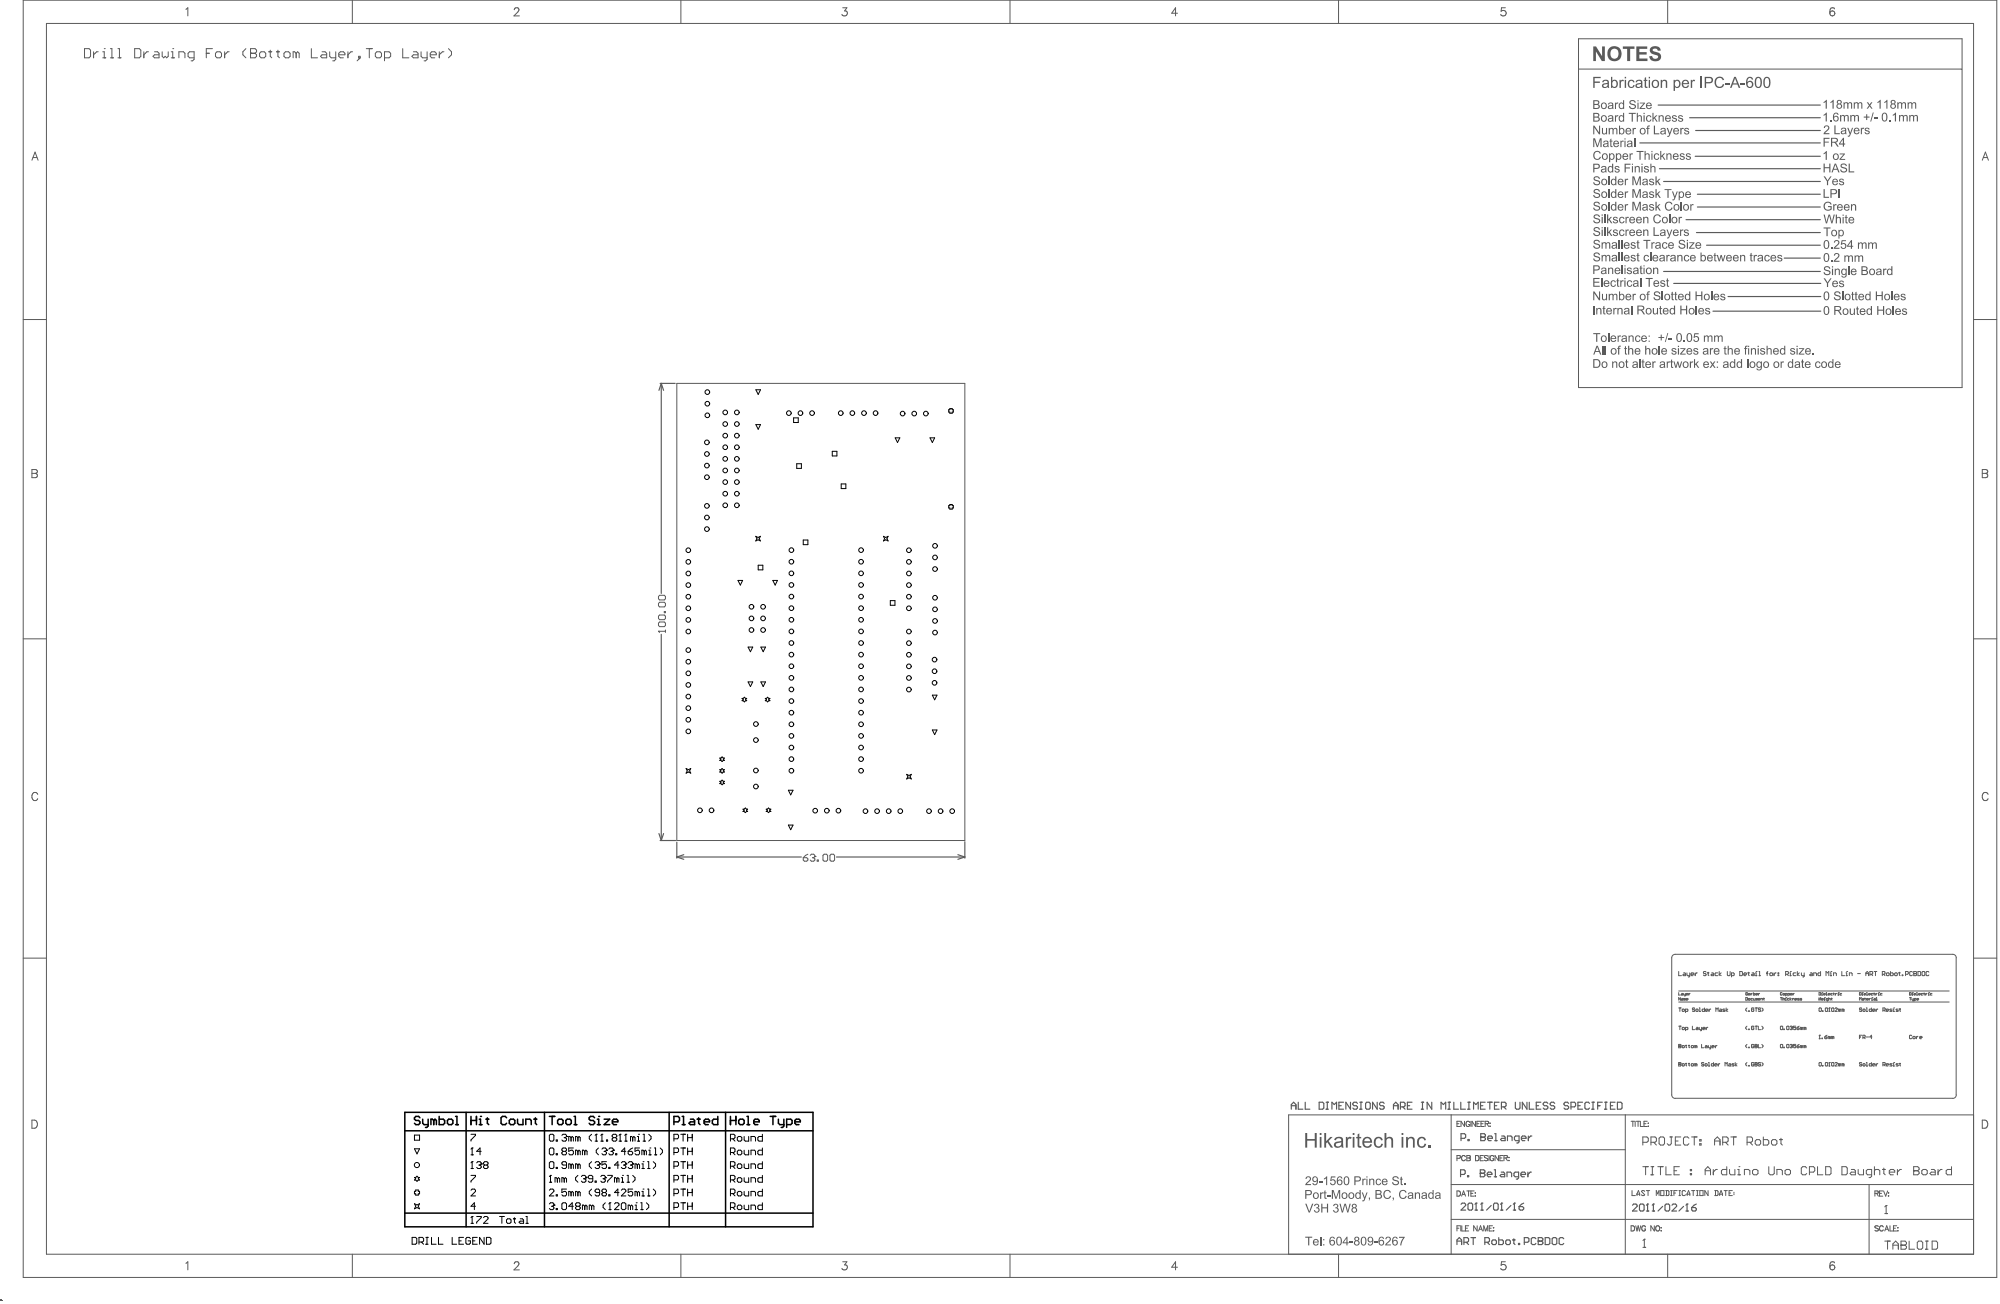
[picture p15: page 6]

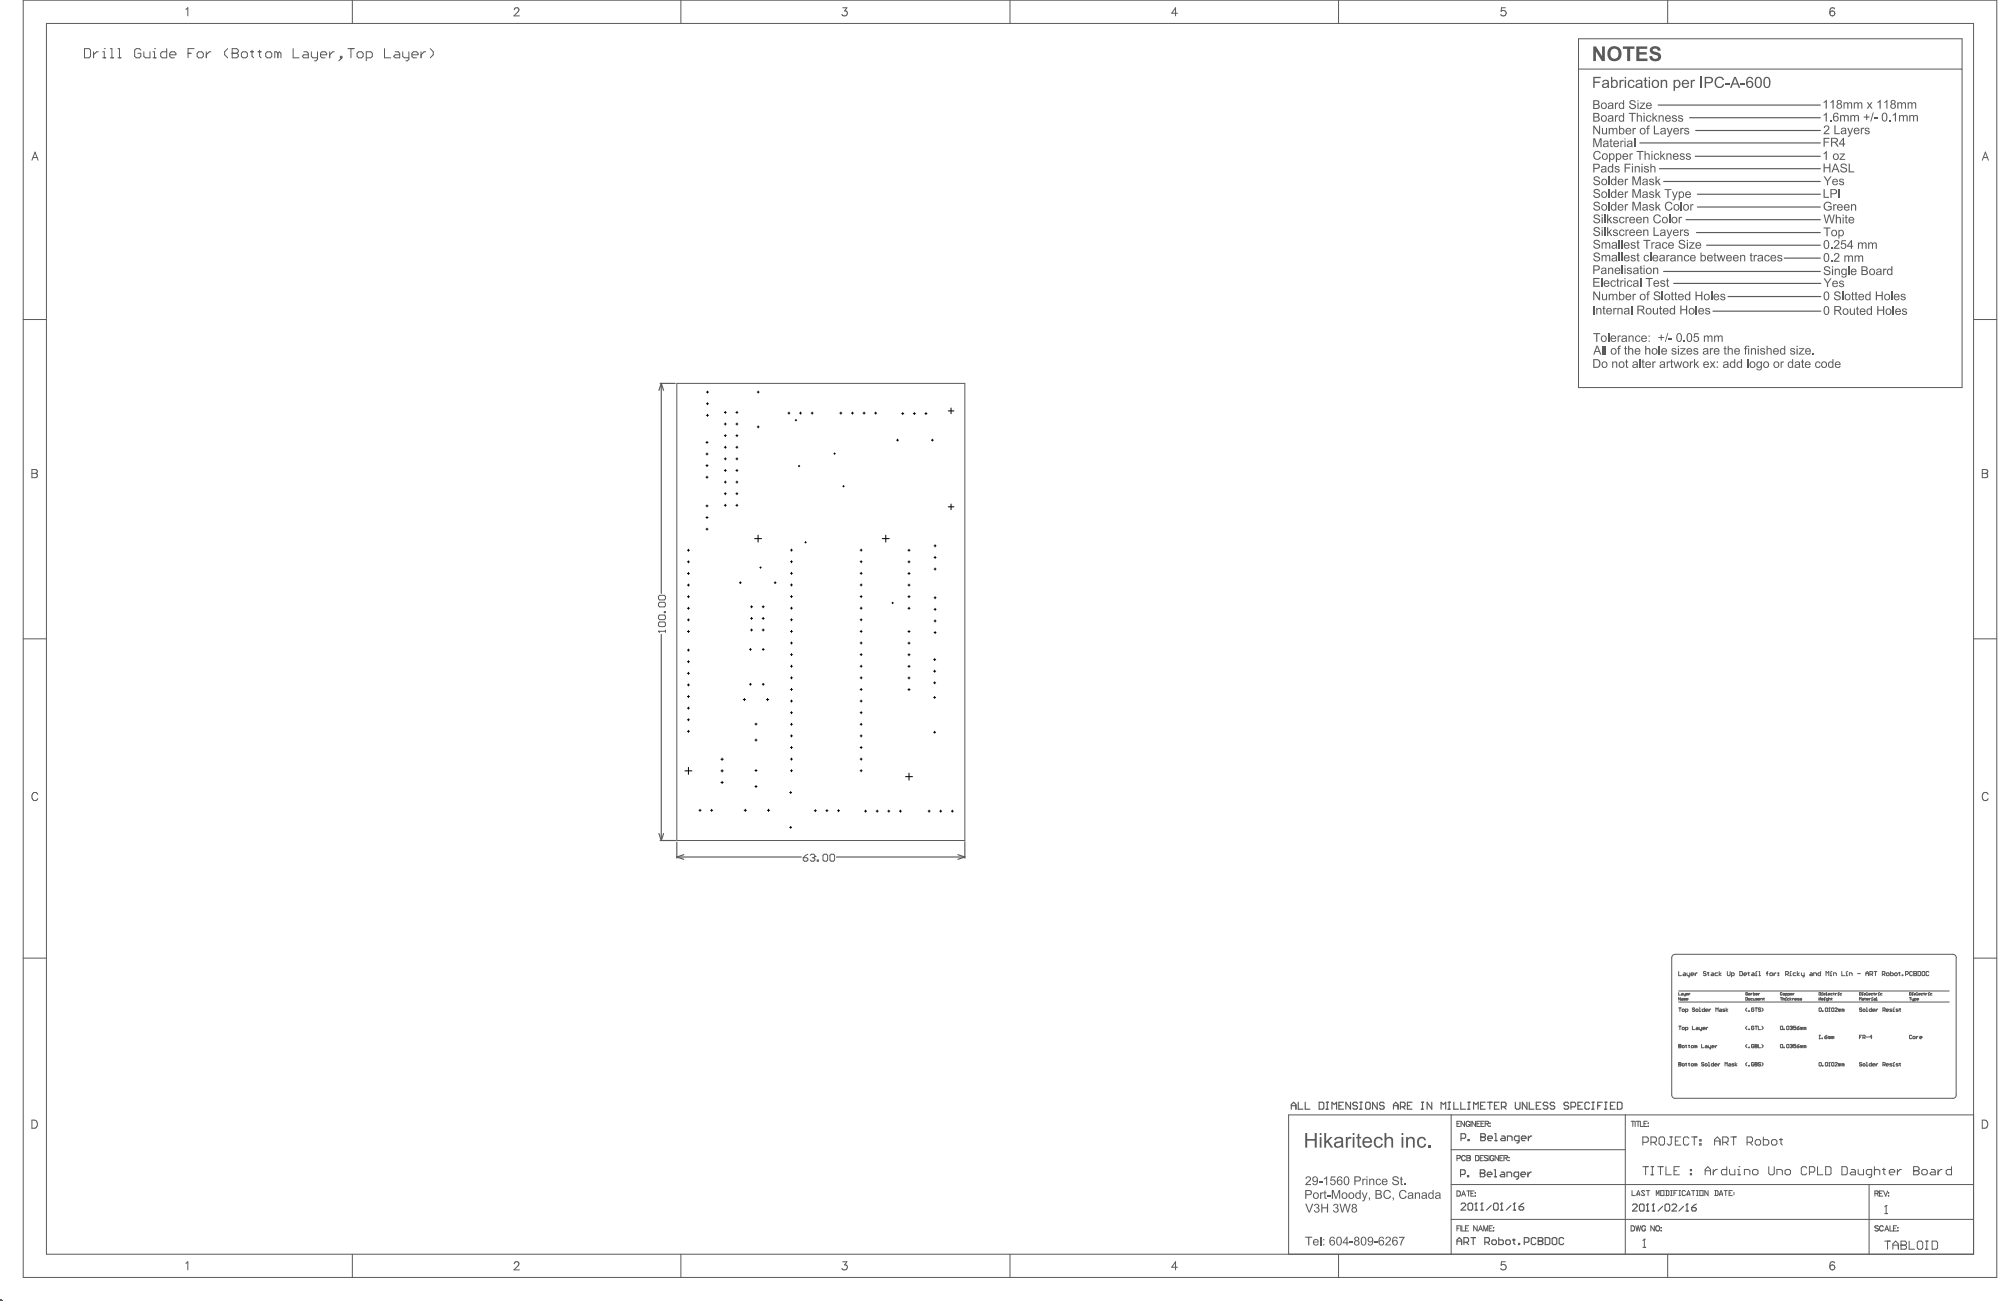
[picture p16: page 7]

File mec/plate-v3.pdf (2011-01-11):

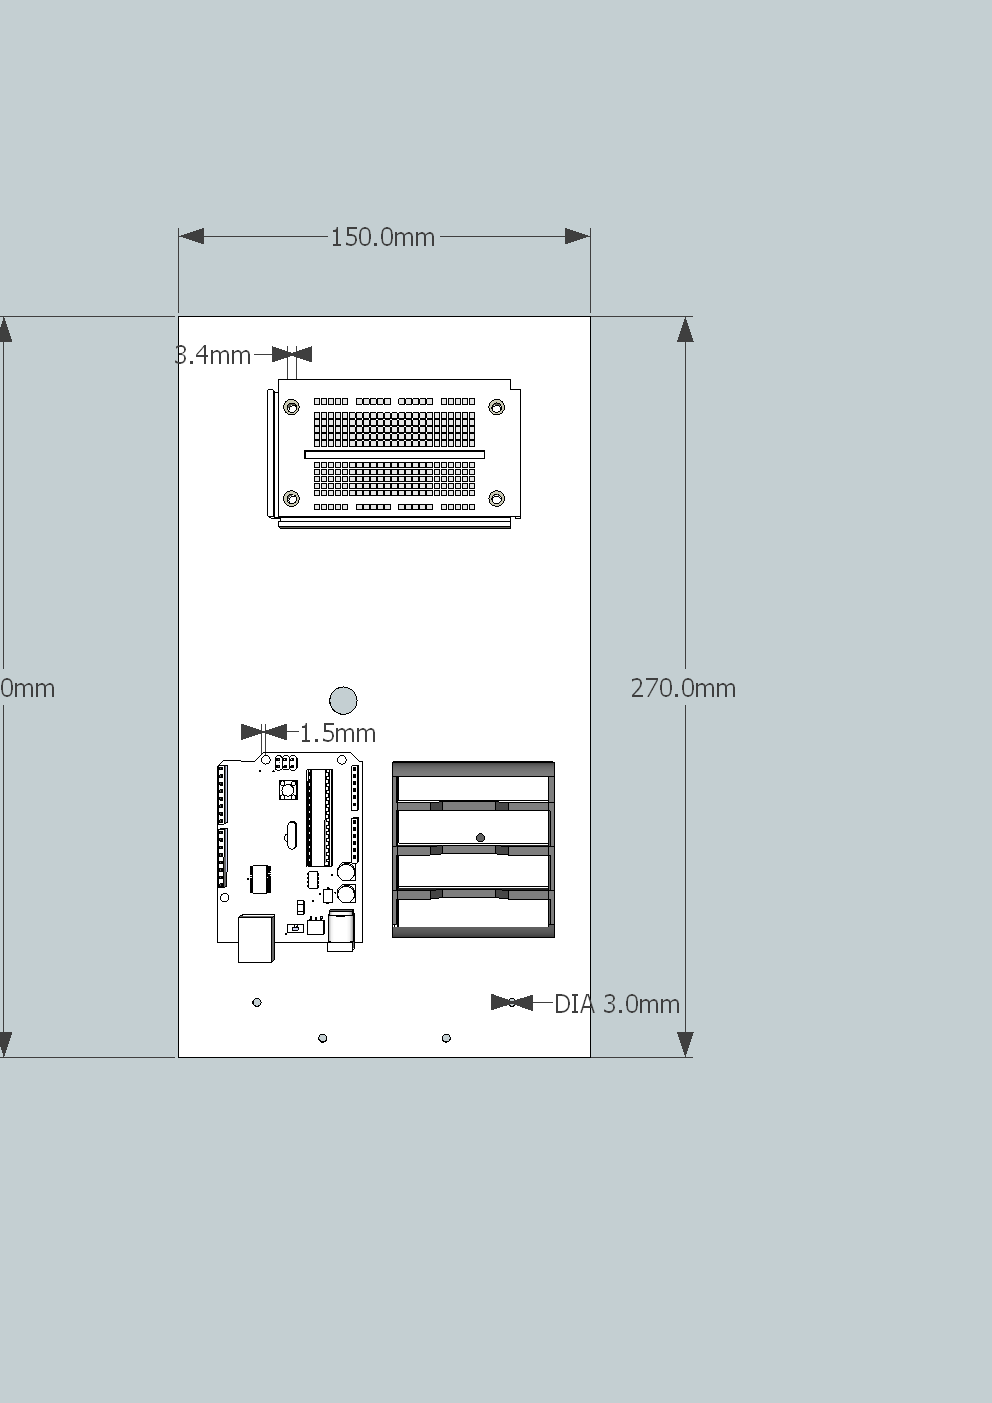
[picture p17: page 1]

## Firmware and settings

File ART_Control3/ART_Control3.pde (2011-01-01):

#include <Ultrasonic.h>
#include <Servo.h> 
#include <limits.h>

enum LOG_LEVELS {
   ERROR,
   INFO,
   DEBUG,
   TRACE,
};
int LOG_LEVEL = DEBUG;

// Arduino pins mapping

// various directions we can go to
const int FORWARD =  2;      // the number of the LED pin
const int REVERSE =  3;  
const int LEFT = 4;  
const int RIGHT =  5;  
// ultrasonic
const int ULTRASONIC_TRIG = 8;
const int ULTRASONIC_ECHO = 9;
// servo
const int SENSOR_SERVO = 13;
// analog adjustments
const int FORWARD_POT = A5;
const int BACKWARD_POT = A4;
// buttons
const int PUSHBUTTON = 7;

/*
We're sweeping the servo either left or right
DFR15 METAL GEAR SERVO
Voltage: +4.8-7.2V
Current: 180mA(4.8V)；220mA（6V）
Speed(no load)：0.17 s/60 degree (4.8V);0.25 s/60 degree (6.0V)
Torque：10Kg·cm(4.8V) 12KG·cm(6V) 15KG·cm(7.2V)
Temperature:0-60 Celcius degree
Size：40.2 x 20.2 x 43.2mm
Weight：48g
*/
const int SERVO_TURN_RATE_PER_SECOND = 100; // 100 = 60/(0.2*3) where 3 is caused by load?

/* 
HC-SR04 Ultrasonic sensor
effectual angle: <15°
ranging distance : 2cm – 500 cm
resolution : 0.3 cm
*/
const int SENSOR_LOOKING_FORWARD_ANGLE = 90; 
// rotating counterclockwise...
const int SENSOR_LOOKING_LEFT_ANGLE = 135; 
const int SENSOR_LOOKING_RIGHT_ANGLE = 45; 
const int SENSOR_ARC_DEGREES = 15; // 180, 90, 15 all divisible by 15
const int MAXIMUM_SENSOR_SERVO_ANGLE = 180;
const int MINIMUM_SENSOR_SERVO_ANGLE = 0;
const int NUMBER_READINGS = MAXIMUM_SENSOR_SERVO_ANGLE/SENSOR_ARC_DEGREES; // 180/15 = 12 reading values in front
const int SENSOR_LOOKING_FORWARD_READING_INDEX = SENSOR_LOOKING_FORWARD_ANGLE/SENSOR_ARC_DEGREES; // 90/15 = 6
const int SENSOR_PRECISION_CM = 1;
const int SENSOR_MAX_RANGE_CM = 500;
// speed of sound at sea level = 340.29 m / s
// spec range is 5m * 2 (return) = 10m
// 10 / 341 = ~0.029
const int SPEED_OF_SOUND_CM_PER_S = 34000;
const int SENSOR_MINIMAL_WAIT_ECHO_MILLIS = (SENSOR_MAX_RANGE_CM*2*1000)/SPEED_OF_SOUND_CM_PER_S;

/*
Robot related information
*/
const int ROBOT_TURN_RATE_PER_SECOND = 90;
const int SAFE_DISTANCE = 75;
const int CRITICAL_DISTANCE = 30;
const int MAX_TIME_UNIT_MILLIS = 3000;
const int MIN_TIME_UNIT_MILLIS = 500;
enum states {
  // start state
  INITIAL = 'I',
  FULL_SWEEP = 'S',
  QUICK_SWEEP = 'Q',
  // dynamic requires fast sensor readings
  DYNAMIC_FORWARD = 'F',
  DYNAMIC_REVERSE = 'B',
  DYNAMIC_TURN = 'T',
  DECISION = 'D',
  // units advancement
  FORWARD_LEFT_UNIT = '1',
  FORWARD_UNIT = '2',
  FORWARD_RIGHT_UNIT = '3',
  REVERSE_LEFT_UNIT = '4',
  REVERSE_UNIT = '5',
  REVERSE_RIGHT_UNIT = '6',
  // decision making
  QUICK_DECISION = '?',
  REVERSE_QUICK_DECISION = '<',
  
  // end state
  STUCK = 'K',
  STOP = '.'
};

// Global variable
// this contains readings from a sweep
int sensor_distance_readings_cm[NUMBER_READINGS];
const int NO_READING = -1;
char current_state = STOP;
// contains target angle
int turn_towards;
int current_max_distance = SAFE_DISTANCE; // needs a value for backward

enum {
  WAIT_FOR_SERVO_TO_TURN,
  WAIT_FOR_ROBOT_TO_TURN,
  WAIT_FOR_ECHO,
  WAIT_FOR_ROBOT_TO_MOVE,
  WAIT_FOR_ROBOT_TO_ADVANCE_UNIT,
  WAIT_FOR_BUTTON_REREAD,
  WAIT_ARRAY_SIZE, // always last...
};

int timed_operation_initiated_millis[WAIT_ARRAY_SIZE];
int timed_operation_desired_wait_millis[WAIT_ARRAY_SIZE];

// variables to store the servo current and desired angle 
int current_sensor_servo_angle = 0;

// Two useful objects...
Servo sensor_servo;  // create servo object to control a servo 
Ultrasonic sensor = Ultrasonic(ULTRASONIC_TRIG, ULTRASONIC_ECHO);

void setup() { 
  // these map to the contact switches on the RF
  pinMode(FORWARD, OUTPUT);     
  pinMode(REVERSE, OUTPUT);    
  pinMode(LEFT, OUTPUT);  
  pinMode(RIGHT, OUTPUT);  
  // input potentiometer
  pinMode(FORWARD_POT, INPUT);
  pinMode(BACKWARD_POT, INPUT);
  //buttons
  pinMode(PUSHBUTTON, INPUT);
  
  full_stop();
  sensor_servo.attach(SENSOR_SERVO);
  for(int i=0; i<WAIT_ARRAY_SIZE; i++) {
    timed_operation_initiated_millis[i] = 0;  
    timed_operation_desired_wait_millis[i] = 0;
  }
  safe_update_servo_position(SENSOR_LOOKING_FORWARD_ANGLE);   
  Serial.begin(9600);
}

/*
Makes sure that exclusive directions are prohibited
*/
void go(int dir) {
  switch(dir) {
  case FORWARD:
    digitalWrite(REVERSE, LOW);
    digitalWrite(FORWARD, HIGH);   
    break;
  case REVERSE:
    digitalWrite(FORWARD, LOW);   
    digitalWrite(REVERSE, HIGH);   
    break;  
  case LEFT:
    digitalWrite(RIGHT, LOW);   
    digitalWrite(LEFT, HIGH);   
    break;
  case RIGHT:
    digitalWrite(LEFT, LOW);   
    digitalWrite(RIGHT, HIGH);   
    break;            
  }
}

void suspend(int dir) {
  digitalWrite(dir, LOW);
}

void full_stop() {
  digitalWrite(FORWARD, LOW);
  digitalWrite(REVERSE, LOW);
  digitalWrite(LEFT, LOW);
  digitalWrite(RIGHT, LOW);
}

/*
record current time to compare to
*/
void start_timed_operation(int index, int duration) {
  timed_operation_initiated_millis[index] = millis();
  timed_operation_desired_wait_millis[index] = duration;
  if(LOG_LEVEL >= TRACE) {
    Serial.print("Timer added type ");
    Serial.print(index);
    Serial.print(" wait in millis:");
    Serial.println(duration);
  }
}

/*
Check whether the timer has expired
if expired, returns true else returns false
*/
boolean timed_operation_expired(int index) {
  int current_time = millis();
  if((current_time - timed_operation_initiated_millis[index]) < timed_operation_desired_wait_millis[index]) {
    return false;
  }
  return true;
}

int expected_wait_millis(int turn_rate, int initial_angle, int desired_angle) {
  int delta;
  if(initial_angle < 0 || desired_angle < 0) { 
    return 0;
  } else if(initial_angle == desired_angle) {
    return 0;
  } else if(initial_angle > desired_angle) {
    delta = initial_angle - desired_angle;
  } else {
    delta = desired_angle - initial_angle;
  }
  return (float(delta)/float(turn_rate))*1000.0;
}

int convert_reading_index(int angle) {
  return angle/SENSOR_ARC_DEGREES;
}

int read_sensor() {
  if(!timed_operation_expired(WAIT_FOR_SERVO_TO_TURN)) {
    return NO_READING;
  }
  
  if(!timed_operation_expired(WAIT_FOR_ECHO)) {
    return NO_READING;
  }
  
  int measured_value = sensor.Ranging(CM);
  
  start_timed_operation(WAIT_FOR_ECHO, SENSOR_MINIMAL_WAIT_ECHO_MILLIS);
  
  int index = convert_reading_index(current_sensor_servo_angle);
  // only update if the value is different beyond precision of sensor
  if(abs(measured_value - sensor_distance_readings_cm[index]) > SENSOR_PRECISION_CM) {
    sensor_distance_readings_cm[index] = measured_value;
  }
  if(LOG_LEVEL >= INFO) {
    Serial.print("Sensor reading:");
    Serial.print(current_sensor_servo_angle);
    Serial.print(":");
    Serial.println(sensor_distance_readings_cm[index]);
  }
  return sensor_distance_readings_cm[index];
}

int get_last_reading_for_angle(int angle) {
  return sensor_distance_readings_cm[convert_reading_index(angle)];
}

int get_forward_time_millis() {
  int max_time = map(analogRead(FORWARD_POT), 0, 1024, MIN_TIME_UNIT_MILLIS, MAX_TIME_UNIT_MILLIS);
  int time = map(current_max_distance, 0, SENSOR_MAX_RANGE_CM, MIN_TIME_UNIT_MILLIS, max_time);
  return time;
}

int get_backward_time_millis() {
  // same logic because we don't have a front sensor...
  int max_time = map(analogRead(BACKWARD_POT), 0, 1024, MIN_TIME_UNIT_MILLIS, MAX_TIME_UNIT_MILLIS);
  int time = map(current_max_distance, 0, SENSOR_MAX_RANGE_CM, MIN_TIME_UNIT_MILLIS, max_time);
  return time;
}

/*
Initialize sweep (setting state and position sensor to be ready)
*/
void init_sweep() {
  current_state = FULL_SWEEP;
  safe_update_servo_position(MINIMUM_SENSOR_SERVO_ANGLE);
}

/*
Read the current angle and store it in the readings array
Find the next angle that has no reading
If found, set the desired angle to that and return false
If not found, returns true
*/
boolean sensor_sweep() {
  // read current value
  if(read_sensor() == NO_READING) {
    return false;
  }

  // we have a valid value, so move to the next  position
  int desired_sensor_servo_angle = current_sensor_servo_angle + SENSOR_ARC_DEGREES;
  
  // we've completed from MINIMUM_SENSOR_SERVO_ANGLE to MAXIMUM_SENSOR_SERVO_ANGLE
  if(desired_sensor_servo_angle > MAXIMUM_SENSOR_SERVO_ANGLE) {
    return true;
  } 
  
  // we always use read_sensor() before reaching here
  update_servo_position(desired_sensor_servo_angle);
  // keep doing the sweep
  return false; 
}

/*
make sure that the servo is at target position before returning
if you don't use this, you need to check yourself that the timer has expired...
*/
void safe_update_servo_position(int desired_sensor_servo_angle) {  
    update_servo_position(desired_sensor_servo_angle);
    while(!timed_operation_expired(WAIT_FOR_SERVO_TO_TURN)) {
      check_button();
    }
}

void update_servo_position(int desired_sensor_servo_angle) {  
  if(current_sensor_servo_angle != desired_sensor_servo_angle) {
    sensor_servo.write(desired_sensor_servo_angle-1);              // tell servo to go to position in variable 'pos' 

    int wait_millis = expected_wait_millis(SERVO_TURN_RATE_PER_SECOND, current_sensor_servo_angle, desired_sensor_servo_angle);
    start_timed_operation(WAIT_FOR_SERVO_TO_TURN, wait_millis);

    current_sensor_servo_angle = desired_sensor_servo_angle;
    if(LOG_LEVEL >= DEBUG) {
      Serial.print("SERVO:");
      Serial.println(desired_sensor_servo_angle);
    }
  }
}

boolean potential_collision() {
  return sensor_distance_readings_cm[SENSOR_LOOKING_FORWARD_READING_INDEX] <= SAFE_DISTANCE;
}

boolean imminent_collision() {
  return sensor_distance_readings_cm[SENSOR_LOOKING_FORWARD_READING_INDEX] <= CRITICAL_DISTANCE;
}

int find_best_direction_degrees() {
  int longest_value = -1;
  int longest_index = -1;
  for(int i=0; i<NUMBER_READINGS; i++) {
    if(sensor_distance_readings_cm[i] > longest_value && sensor_distance_readings_cm[i] >= SAFE_DISTANCE) {
      longest_value = sensor_distance_readings_cm[i];
      longest_index = i;
    }
  }
  if(longest_index != -1) {
    return longest_index * SENSOR_ARC_DEGREES;
  }
  return NO_READING;
}

/*
Find out where we get the best distance range and go towards that
If all the distances in front are unsafe, return REVERSE
*/
int quick_decision() {
  // one of the value has been updated, check to see if we should go left or right 
  // or just keep going forward
  int left_value = get_last_reading_for_angle(SENSOR_LOOKING_LEFT_ANGLE);
  int right_value = get_last_reading_for_angle(SENSOR_LOOKING_RIGHT_ANGLE);
  int forward_value = get_last_reading_for_angle(SENSOR_LOOKING_FORWARD_ANGLE);
  
  if(left_value > forward_value && left_value > right_value) {
    if(left_value < SAFE_DISTANCE) {
      return REVERSE;
    }
    current_max_distance = left_value;
    return LEFT;
  } else if(right_value > forward_value && right_value > left_value) {
    if(right_value < SAFE_DISTANCE) {
      return REVERSE;
    }
    current_max_distance = right_value;
    return RIGHT;
  } else {
    if(forward_value < SAFE_DISTANCE) {
      return REVERSE; 
    }
    current_max_distance = forward_value;
    return FORWARD;
  }
}

/*
completes once the sensor has readings left, right and center
*/
boolean check_left;
int quick_sweep_number_readings = 0; // use modulo 4 to get every three readings
void init_quick_sweep() {
  full_stop();
  check_left = true; // always want to go left first
  current_state = QUICK_SWEEP;
  safe_update_servo_position(SENSOR_LOOKING_FORWARD_ANGLE);
}

boolean quick_sweep() {
    // we check if we have an updated value here
    if(read_sensor() != NO_READING) {
      quick_sweep_number_readings++;
      // we have an updated value, if it's a center value
      // move the servo to get left and right readings
      if(current_sensor_servo_angle == SENSOR_LOOKING_FORWARD_ANGLE) {
        // go left or right depending on check_left
        if(check_left) {
          // inside read_sensor() which guarantees servo timer expired
          update_servo_position(SENSOR_LOOKING_LEFT_ANGLE);
        } else {  
          // inside read_sensor() which guarantees servo timer expired
          update_servo_position(SENSOR_LOOKING_RIGHT_ANGLE);
        }
      } else {
        // check left toggles between true and false here
        check_left = !check_left;
        // return to center; this mean we read twice as often forward than left or right
        update_servo_position(SENSOR_LOOKING_FORWARD_ANGLE);
      }
      return true;
    }
    return false;
}

void init_turn() {
  full_stop();
  current_state = DYNAMIC_TURN;
  safe_update_servo_position(SENSOR_LOOKING_FORWARD_ANGLE);
  // 0-90 is to the right
  if(turn_towards < SENSOR_LOOKING_FORWARD_ANGLE) {
    go(RIGHT);
  } 
  // 90 to 180 is to the left
  else {
    go(LEFT);
  }
  go(FORWARD);
  int expected_wait = expected_wait_millis(ROBOT_TURN_RATE_PER_SECOND, SENSOR_LOOKING_FORWARD_ANGLE, turn_towards);
  start_timed_operation(WAIT_FOR_ROBOT_TO_TURN, expected_wait);
  if(LOG_LEVEL >= DEBUG) {
    Serial.print("Waiting for robot to turn millis: ");
    Serial.println(expected_wait);
  }
}

void init_go_forward() {
  full_stop();
  current_state = DYNAMIC_FORWARD;
  safe_update_servo_position(SENSOR_LOOKING_FORWARD_ANGLE);
}

void init_decision() {
  full_stop();
  current_state = DECISION;
  safe_update_servo_position(SENSOR_LOOKING_FORWARD_ANGLE);
}

void init_stuck() {
  full_stop();
  current_state = STUCK;
}

void init_quick_decision() {
  full_stop();
  current_state = QUICK_DECISION;
}
int last_forward_state = FORWARD_UNIT;
void init_direction_unit(int decision) {
  full_stop();
  if(decision == REVERSE) {
    current_state = REVERSE_QUICK_DECISION;
    return; // switching state
  }
  
  switch(decision) {
    case LEFT:
      current_state = FORWARD_LEFT_UNIT;
      go(LEFT);
      break;
    case RIGHT:
      current_state = FORWARD_RIGHT_UNIT;
      go(RIGHT);
      break;
    case FORWARD:
      current_state = FORWARD_UNIT;
      break;
    default:
      if(LOG_LEVEL >= ERROR) {
        Serial.print("BAD STATE IN init_direction_unit:");
        Serial.println(decision);
      }
      break;
  }
  last_forward_state = current_state;
  int forward_time_millis = get_forward_time_millis();
  if(LOG_LEVEL>=INFO) {
    Serial.print("Will move for (ms): ");
    Serial.println(forward_time_millis);
  }
  start_timed_operation(WAIT_FOR_ROBOT_TO_ADVANCE_UNIT, forward_time_millis);
  go(FORWARD);
}

void init_direction_reverse_unit(int dir) {  
  full_stop();
  switch(dir) {
    case LEFT:
      current_state = REVERSE_LEFT_UNIT;
      go(LEFT); 
      break;
    case RIGHT:
      current_state = REVERSE_RIGHT_UNIT;
      go(RIGHT); 
      break;
    case REVERSE:
      current_state = REVERSE_UNIT;
      break;
    default:
      if(LOG_LEVEL >= ERROR) {
        Serial.print("BAD STATE IN init_direction_reverse_unit:");
        Serial.println(dir);
      }
      break;
  }
  int backward_time_millis = get_backward_time_millis();
  if(LOG_LEVEL>=INFO) {
    Serial.print("Will move for (ms): ");
    Serial.println(backward_time_millis);
  }
  start_timed_operation(WAIT_FOR_ROBOT_TO_ADVANCE_UNIT, backward_time_millis);
  go(REVERSE);
}

void check_button() {
  // read the state of the pushbutton value:
  if(!timed_operation_expired(WAIT_FOR_BUTTON_REREAD)) {
    return;
  }
  int buttonState = digitalRead(PUSHBUTTON);
  // check if the pushbutton is pressed.
  // if it is, the buttonState is HIGH:
  if (buttonState == HIGH) {     
    if(LOG_LEVEL >= INFO) {
      Serial.println("Button pressed!");
    }
    if(current_state == STOP) {
      current_state = INITIAL;
    } else {
      full_stop();
      current_state = STOP;
    }
    start_timed_operation(WAIT_FOR_BUTTON_REREAD, 1000);
  } 
}

void loop(){
  int initial_state = current_state;
  check_button();
  switch(current_state) {
  // initial; this initiates what type of sub-state-machine we want to use
  // dynamic: more complex states that are supposed to adjust while moving
  // unit: move one unit, scan, decide, move one unit, scan, decide, move one unit...
  case INITIAL:
    // wait for the first reading...
    if(read_sensor() != NO_READING) {
      init_quick_sweep(); // change this to change sub-state-machine
    }
    break;
    
  // dynamic states
  case FULL_SWEEP:
    if(sensor_sweep()) {
      // sweep completed, decision time!
      init_decision();
    } // else keep sweeping!
    break;
  case DYNAMIC_FORWARD:
    if(potential_collision()) {
      // we're going to crash into something, stop and find an alternative
      init_sweep();
    } else { 
      go(FORWARD);
      if(quick_sweep()) {
        suspend(LEFT);
        suspend(RIGHT);
        int decision = quick_decision();
        if(decision == REVERSE) {
          init_stuck();
        } else {
          go(decision);
        }
      }
    }
    break;
  case DECISION:
    // we want to turn towards the longest opening
    turn_towards = find_best_direction_degrees();
    if(turn_towards != NO_READING) {
      init_turn();
    } 
    else {
      init_stuck();
    }
    break;
  case DYNAMIC_TURN:
    read_sensor();
    if(imminent_collision()) {
      init_stuck();
    }
    if(timed_operation_expired(WAIT_FOR_ROBOT_TO_TURN)) {
      // we've turned! reset and try to move forward now
      init_go_forward();
    }
    break;
  case STUCK:
    go(REVERSE);
    if(quick_sweep()) {
      if(!potential_collision()) {
        init_sweep();
      }
    }
    break;
  
  // unit behavior
  case QUICK_SWEEP:
    if(quick_sweep()) {
      // sweep has read one more reading
      if(quick_sweep_number_readings % 4 == 0) {
        // we've completed three readings
        init_quick_decision();
      }
    }
    break;
  case QUICK_DECISION:
    init_direction_unit(quick_decision());
    break;
  case REVERSE_QUICK_DECISION:
    // no sensors to tell us if we can reverse
    // or what direction to prefer so we always do...
    switch(last_forward_state) { 
      case FORWARD_LEFT_UNIT:
        init_direction_reverse_unit(RIGHT);
        break;
      case FORWARD_RIGHT_UNIT:
        init_direction_reverse_unit(LEFT);
        break;
      case FORWARD_UNIT:
        init_direction_reverse_unit(REVERSE);
        break;
    }

    break;
  case FORWARD_UNIT:
  case FORWARD_LEFT_UNIT:
  case FORWARD_RIGHT_UNIT:
  case REVERSE_UNIT:
  case REVERSE_LEFT_UNIT:
  case REVERSE_RIGHT_UNIT:
    // all directions work the same: we wait!
    if(timed_operation_expired(WAIT_FOR_ROBOT_TO_ADVANCE_UNIT)) {
      init_quick_sweep();
    }
    break;
  case STOP:
    // do nothing...
    if(LOG_LEVEL >= INFO) {
      if(millis() % 1000 == 0) {
        Serial.print('.');
      }
    }
    break;
  default:
    if(LOG_LEVEL >= ERROR) { 
        Serial.print("BAD STATE IN main loop:");
        Serial.println(current_state);
    }
    break;
  }

  if(initial_state != current_state) {
    if(LOG_LEVEL >= INFO) {
      Serial.print("INITIAL STATE:");
      Serial.print((char)initial_state);
      Serial.print(" FINAL STATE:");
      Serial.println((char)current_state);
    }
  }
}

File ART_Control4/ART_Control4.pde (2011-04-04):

/*****************************************************************************
 * ART CONTROLLER
 * 
 * Copyright 2011 Ricky Ng-Adam
 * 
 * Licensed under the Apache License, Version 2.0 (the "License");
 * you may not use this file except in compliance with the License.
 * You may obtain a copy of the License at
 * 
 * http://www.apache.org/licenses/LICENSE-2.0
 * 
 * Unless required by applicable law or agreed to in writing, software
 * distributed under the License is distributed on an "AS IS" BASIS,
 * WITHOUT WARRANTIES OR CONDITIONS OF ANY KIND, either express or implied.
 * See the License for the specific language governing permissions and
 * limitations under the License.
 *****************************************************************************/

/*****************************************************************************
 * ARDUINO LIBS
 *****************************************************************************/
#include <Servo.h> 
#include <limits.h>

/*****************************************************************************
 * NY LIBS
 *****************************************************************************/
#include "types.h"
#include "Ultrasonic.h"

/*****************************************************************************
 * LOGGING
 *****************************************************************************/
enum telemetry_types {
  ULTRASONIC_SENSORS,
  STATE_CHANGE,
  SENSOR_SERVO_POSITION_CHANGE,
  CAR_GO_COMMAND,
  CAR_SUSPEND_COMMAND,
  MAX_TELEMETRY_TYPE,
};

/*char* telemetry_types_names[] = {
 "ULTRASONIC_SENSORS",
 "STATE_CHANGE",
 "SENSOR_SERVO_POSITION_CHANGE",
 "CAR_GO_COMMAND",
 "CAR_SUSPEND_COMMAND",
 };*/

#define DEBUG
#define TELEMETRY
#define ERROR_SERIAL_LOGGING   
#undef TRACE_SERIAL_LOGGING  

#ifdef DEBUG
#define DEBUG_PRINT(str)    \
    Serial.print(millis());     \
    Serial.print(": ");    \
    Serial.print(__FUNCTION__); \
    Serial.print(':');      \
    Serial.print(__LINE__);     \
    Serial.print(' ');      \
    Serial.println(str);
#else
#define DEBUG_PRINT(str)
#endif 

#ifdef TELEMETRY
#define LOG_TELEMETRY(type, source, value) \
Serial.print("|"); \
Serial.print(millis()); \
Serial.print(","); \
Serial.print((int)type); \
Serial.print(","); \
Serial.print((int)source); \
Serial.print(","); \
Serial.println((int)value);  
#else
#define LOG_TELEMETRY(type, source, value)
#endif

#ifdef ERROR_SERIAL_LOGGING    
#define LOG_BAD_STATE(value) \
Serial.print(millis()); \
Serial.print(": "); \
Serial.print(__FUNCTION__); \
Serial.print(':'); \
Serial.print(__LINE__); \
Serial.print(' '); \
Serial.println((int)value);
#define LOG_ERROR(message, context, expected, actual) \
Serial.print("ERROR:"); \
Serial.print(millis()); \
Serial.print(":"); \
Serial.print(message); \
Serial.print(" context:"); \
Serial.print((int)context); \
Serial.print(" expected:"); \
Serial.print((int)expected); \
Serial.print(" actual:"); \
Serial.println((int)actual);     
#else
#define LOG_ERROR(message, source, expected, actual)
#define LOG_BAD_STATE(value)
#endif

#ifdef TRACE_SERIAL_LOGGING    
#define LOG_TRACE4(message1, value1, message2, value2) \
Serial.print("TRACE:"); \
Serial.print(millis()); \
Serial.print(":"); \
Serial.print(message1); \
Serial.print((int)value1); \
Serial.print(message2); \
Serial.println((int)value2);   
#define LOG_TRACE2(message1, value1) \
Serial.print("TRACE:"); \
Serial.print(millis()); \
Serial.print(":"); \
Serial.print(message1); \
Serial.println((int)value1); 
#else
#define LOG_TRACE4(message1, value1, message2, value2)
#define LOG_TRACE2(message1, value1)
#endif


/*****************************************************************************
 * ARDUINO PINS MAPPING
 *****************************************************************************/
// ultrasonic
pin_t ULTRASONIC_REVERSE_TRIG = 2;
pin_t ULTRASONIC_REVERSE_ECHO = 3;
pin_t ULTRASONIC_FORWARD_TRIG = 4;
pin_t ULTRASONIC_FORWARD_ECHO = 5;
// various directions we can go to
pin_t FORWARD_PIN =  6;      // the number of the LED pin
pin_t REVERSE_PIN =  7;  
pin_t LEFT_PIN = 8;  
pin_t RIGHT_PIN =  9;  
pin_t PUSHBUTTON_PIN = 10;
// servo
pin_t SENSOR_SERVO_PIN = 12;

/*****************************************************************************
 * TIMING RELATED
 *****************************************************************************/
enum waits_types {
  WAIT_FOR_SERVO_TO_TURN,
  WAIT_FOR_ECHO,
  WAIT_FOR_ROBOT_TO_MOVE,
  WAIT_FOR_BUTTON_REREAD,
  WAIT_ARRAY_SIZE, // always last...
};

time_ms_t timed_operation_initiated_millis[WAIT_ARRAY_SIZE]; // 4 bytes * 4 = 16 bytes
duration_ms_t timed_operation_desired_wait_millis[WAIT_ARRAY_SIZE]; // 2 bytes * 2 = 4 bytes

/*
record current time to compare to
 */
void start_timed_operation(enum_t index, duration_ms_t duration) {
  timed_operation_initiated_millis[index] = millis();
  timed_operation_desired_wait_millis[index] = duration;
  LOG_TRACE4("Timer added type ", index, " wait in millis:", duration);
}

/*
Check whether the timer has expired
 if expired, returns true else returns false
 */
boolean timed_operation_expired(enum_t index) {
  if((millis() - timed_operation_initiated_millis[index]) < timed_operation_desired_wait_millis[index]) {
    //DEBUG_PRINT("not expired");
    return false;
  }
  //DEBUG_PRINT("expired");
  return true;
}

/*****************************************************************************
 * SENSOR SERVO
 *****************************************************************************/
/*
We're sweeping the servo either left or right
 DFR15 METAL GEAR SERVO
 Voltage: +4.8-7.2V
 Current: 180mA(4.8V)；220mA（6V）
 Speed(no load)：0.17 s/60 degree (4.8V);0.25 s/60 degree (6.0V)
 Torque：10Kg·cm(4.8V) 12KG·cm(6V) 15KG·cm(7.2V)
 Temperature:0-60 Celcius degree
 Size：40.2 x 20.2 x 43.2mm
 Weight：48g
 */
constant_t SERVO_TURN_RATE_MS_PER_DEGREE = 3; 
Servo sensor_servo;   

duration_ms_t expected_wait_millis(turn_rate_t turn_rate, angle_t initial_angle, angle_t desired_angle) {
  angle_t delta;
  duration_ms_t return_value;
  if(initial_angle == desired_angle) {
    return_value = 0;
  } 
  else if(initial_angle > desired_angle) {
    return_value = turn_rate * (initial_angle - desired_angle);
  } 
  else {
    return_value = turn_rate * (desired_angle - initial_angle);
  }
  return return_value;
}
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

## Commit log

2010-12-29 -Add new configuration control (two infrared front sensors crossing beams) -Add the RF control experiment
2010-12-30 Servo/Sensor is by default 90 degrees to the front
    In static tests, when an object is in front, the sensor sweeps the forward 180 degrees at 15 degrees increment
    If there is an obstruction in front within 50 cm, it stops.
    It then performs a sweep again and tries turning towards the longest distance found.
    If it finds an opening, it initiates a turn.
2010-12-31 Sweeping activates at proper times Delay to let the servo sweeping the servo reach it's target position Delay to take into echoes to the acoustic sensor Delay to let the robot turn adequately
2010-12-31 Sensor wasn't completing full sweep
2010-12-31 This version has problem as it constantly switches back to sweep...
    [ART_Control3.pde]
2010-12-31 quick sweep + precise sweep seem to work (values just get printed when they change enough)
2010-12-31 fix missing last 180 degrees reading... added various log levels
    [ART_Control3.pde]
2010-12-31 added reverse when getting stuck...
    [ART_Control3.pde]
2011-01-01 two bugs fixed while testing static: -case missing (fall through everytime) -last right reading of quick sweep not actually read
    [ART_Control3.pde]
2011-01-01 fix bug: always returning reverse (if ... ;)
    [ART_Control3.pde]
2011-01-01 same missing case in switch statement error in other function!
    [ART_Control3.pde]
2011-01-01 added reverse with direction based on last forward direction
    [ART_Control3.pde]
2011-01-01 added potentiometers to parametrize forward/backward time unit easily added push button to start/stop robot
2011-01-01 two bugs fixed: pushbutton sometimes not checked while servo is moving... stopping should also stop any pass RF order with full_stop()...
    [ART_Control3.pde]
2011-01-01 revert change to ART_Control3 move ART_Control4 to right file modify ART_Control4 to support sensor forward and backward
    [ART_Control3.pde, ART_Control4.pde]
2011-01-01 was reading forward sensor instead of reverse!
    [ART_Control4.pde]
2011-01-01 remove useless states change pin (13 is LED) fix bug REVERSE -> REVERSE_UNIT
    [ART_Control4.pde]
2011-01-01 use a class/struct for sensor readings processing
2011-01-01 add reverse assist to forward turn
    [ART_Control4.pde]
2011-01-01 use concept of safe versus critical distance favor going backward if below safe distance; also, fix so that the concept of reverse right or left is taken care just at the lowest level...
    [ART_Control4.pde]
2011-01-01 safe distance check was very wrong...
    [ART_Control4.pde]
2011-01-02 missing reading the actual value from the side sensor...
    [ART_Control4.pde]
2011-01-02 actually handle SIDE in quick_decision consistent logging for unhandled default switch statement
2011-01-02 obvious bug where I wasn't looking at reverse properly...
    [ART_Control4.pde]
2011-01-09 reorganize by robot hierarchy, introduce SMALL_TURN_CW AND SMALL_TURN_CCW states, single array to get sensor readings. (compiles, not tested or inspected)
2011-01-09 Record telemetry and keep track of current motor states
2011-01-09 Crashes; everytime I press the button, the Arduino resets! Think there might be something related to my use of unsigned long
    [ART_Control4.pde]
2011-01-09 fix some of the re-introduced bugs (set servo delay after moving it, incorrect sweep order, serial using char instead of value)
    [ART_Control4.pde]
2011-01-09 Fix stucked state for small radius turn and just plain incorrect code
    [ART_Control4.pde]
2011-01-09 kinda works but not very dynamic behavior; seems to stop for too long
    [ART_Control4.pde]
2011-01-09 add libraries distributed with the HC-SR04 sensor
2011-01-11 additional files created during the project so far
    [ART-platform4.fz, ART.sch, robot-car-base-plate-with-arduino-v2.skp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]
2011-01-11 Modify some of the stranger constructs in Ultrasonic and get rid of the !@#$% imperial system.
2011-01-11 ART5 initial setup
    [ART.sch, BOM.ods]
2011-01-12 git mv the Fritzing design to the right place and save latest changes in open apps
    [ART.fz, ART.sch, BOM.ods]
2011-01-12 cleaning up directory organization under ELE and add new Fritzing part (RFC-1100A) to the ART schematic
    [ART.fz]
2011-01-12 keep informaton for XC9536 in DIP package
    [ART.fz]
2011-01-12 copyright notice and pending changes in PCB
2011-01-13 wishlist components
    [wishlist.ods]
2011-01-14 updated schematic with sensor placement and attempt at schematic/PCB
    [ART.fz]
2011-01-14 semi-decent PCB
    [ART.fz]
2011-01-14 Most connections routed
    [ART.fz]
2011-01-14 before routing
    [ART.fz]
2011-01-14 Updated shield with all connectors
    [ART-shield.fz, ART.fz]
2011-01-14 a few too many jump wires, but it works...
    [ART-shield.fz]
2011-01-15 latest version of ART-shield before changing the RF transceiver to be standing up
    [ART-shield.fz]
2011-01-15 fix incorrect wiring for SPI...
    [ART-shield.fz]
2011-01-15 better routing (two jumper wires) but without holes
    [ART-shield.fz]
2011-01-15 with screwholes for RF
    [ART-shield.fz]
2011-01-15 make sure headers clear the RF card in case I was to pile on stuff on the stackable headers
    [ART-shield.fz]
2011-01-15 more tiny adjustments
    [ART-shield.fz]
2011-01-15 More accurate alignment of RF holes
    [ART-shield.fz]
2011-01-15 overlapping parts
    [ART-shield.fz]
2011-01-15 tiny changes
    [ART-shield.fz]
2011-01-15 left-over changes in opened editors
    [BOM.ods, wishlist.ods]
2011-01-16 needs some more work, just a basic outline of the registers for now
    [ART.sch]
2011-01-20 This is the daughter board PCB for the Arduino
    [Ricky and Min Lin - ART Robot.PCBDOC, Ricky and Min Lin - ART Robot.SchDoc]
2011-01-22 Textual state output and temperature state selection
2011-01-23 Seems to be exchanging a preamble with something - tiny problem, the NetUSB is not connected!
    [RFTest.pde]
2011-01-23 fix the issue with status being returned: was using strobe (READ_SINGLE) instead of correct command to read register (READ_BURST)!
    [RFTest.pde]
2011-01-23 still unable to get the NetUSB and the RFC1100A to work together...
    cleaned up some of the data structure
    delays in rx() is not working
    [RFTest.pde]
2011-01-29 Updated schematic for revision
2011-01-29 Update the PCB with servo headers and designators (to Review)
2011-02-17 Schematic Completed with PCB Routed Done. Gerber are ready.
    [Ricky and Min Lin - ART Robot.PCBDOC, Ricky and Min Lin - ART Robot.SchDoc]
2011-02-17 New PCB, Gerber and Schematic to review before manufacturing.
    [ART Robot.DRL, ART Robot.GBL, ART Robot.GBO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]
2011-04-04 use of counters to determine behavior (forward, reverse, left, right)
    -still runs into stuff at full speed but mostly interesting behavior nonetheless...
    -tends to "hesitate" between left and right.
    [Controller.pde]
2011-04-04 adding interrupt control
2011-04-05 bill of material and project overview...
    [BOM.ods]
2011-04-09 background on project
    [BOM.ods]
2011-06-20 pdf version of bill of material
2011-07-02 compiles and uploads to ATMega board
2011-07-03 Initial user interface with ADK hookups
    [proguard.cfg]
2011-07-03 updated firmware for ART device
    [ART.sch]
2011-07-03 fix bad updates because of only looking at sensor going low...
    [device.pde]
2011-07-08 some test projects and latest changes
    [proguard.cfg]
2011-07-09 the new binaries; kind of work, but very buggy.
    [proguard.cfg]
2011-07-09 Fixed slowness introduced by putting robot update in the video update thread...
2011-07-11 competition changes and fixes (sadly, defeated by a bad USB cable...)
